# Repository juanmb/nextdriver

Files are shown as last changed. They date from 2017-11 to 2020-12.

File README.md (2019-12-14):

# NexStar Controller

A USB controller for [Celestron](https://www.celestron.com/collections/astronomy)
telescopes using the NexStar AUX protocol.

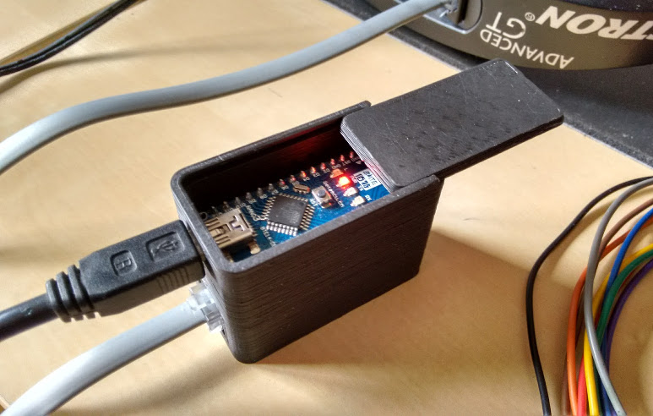
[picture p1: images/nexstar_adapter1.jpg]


## Description

This is a USB controller for Celestron NexStar AUX protocol implemented in Arduino.
It substitutes the hand controller, receiving the commands from the PC (HC procotol)
and communicating with the mount (AUX protocol).



Documentation on the NexStar HC and Aux protocols:

 * [NexStar HC Protocol](http://www.nexstarsite.com/download/manuals/NexStarCommunicationProtocolV1.2.zip)
 * [NexStar AUX Protocol](http://www.paquettefamily.ca/nexstar/NexStar_AUX_Commands_10.pdf)

## Features

 * Get/set location and time
 * Sync
 * Goto (equatorial and horizontal coordinates)
 * Tracking on/off
 * Meridian flip
 * Above-the-horizon limit

TODO:

 * RTC support
 * Homing switches
 * Hibernate/wakeup
 * Support for South hemisphere
 * Support for alt-az mounts

## Limitations

Currently, only equatorial mounts in the North hemisphere are supported.

## Required libraries

 * [Time](https://github.com/PaulStoffregen/Time)
 * [AccelStepper](https://github.com/waspinator/AccelStepper.git)

The library AstroLib, wich is part of this project, must be installed in the
Arduino libraries directory.

## Compiling

The provided Makefile requires [Arduino-Makefile](https://github.com/sudar/Arduino-Makefile)
to work. In Debian/Ubuntu/Mint, you can install it with

    sudo apt install arduino-mk

If you downloaded `Arduino-Makefile` to a custom location (other than
`/usr/share/arduino`), you must indicate the correct directory by modifying
the `ARDMK_DIR` variable in the `Makefile.avr` or `Makefile.sam`.

The code can be compiled and uploaded to the Arduino board using

    make
    make upload

Of course, you can also program the Arduino board using the Arduino IDE.

### Compiling for Arduino Due

Download the toolchain for SAM boards using the Boards Manager in the Arduino IDE.

Comment the line `include Makefile.avr` and discomment the line
`include Makefile.sam` in the `Makefile`.

## Schematics

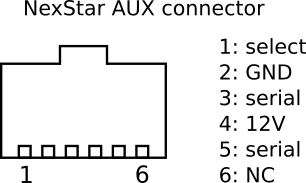
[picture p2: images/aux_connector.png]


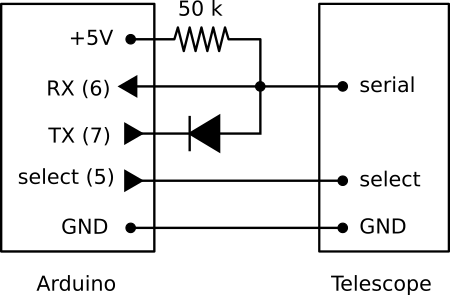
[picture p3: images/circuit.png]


## Enclosure

The CAD directory contains an STL model of the enclosure I use, which was
created with openSCAD. It requires an Arduino Nano and a small prototype
board. The resistor, the diode and the modular connector shown in the
schematics are mounted in the prototype board.

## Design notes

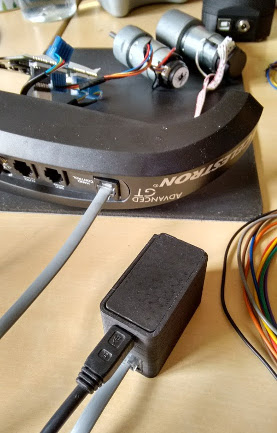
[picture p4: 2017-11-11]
images/nexstar_adapter2.jpg

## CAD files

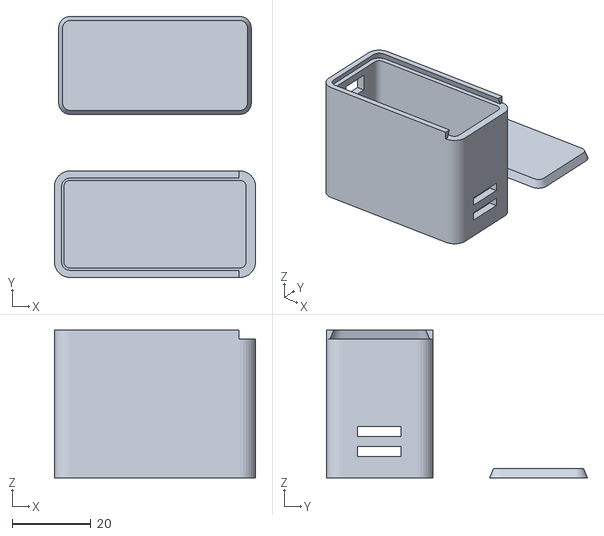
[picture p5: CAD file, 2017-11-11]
CAD/nexstar_adapter.stl
51.0 x 66.1 x 37.4

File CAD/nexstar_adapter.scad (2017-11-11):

thickness = 2.4;
size = [46+2*thickness, 22+2*thickness, 35];    // outer dimensions
connSize = [13, 13, 12.0];
usbSize = [8.5, 8.5, 5];
pcbThickness = 1.6;
connSize2 = [11, 11, 2.5];

$fn = 32;


module box(size, thickness, radius=4, tolerance=0.2, lid=false) {
    // some shorter aliases
    t = tolerance;
    th = thickness;
    r = radius;
    d = 2*r;

    // lid slope
    slope1 = 1.5;
    slope2 = 0.5;

    module outerCorner(x, y) {
        translate([(size[0] - d + t)*x, (size[1] - d + t)*y, 0])
            cylinder(size[2] + th, r=r);
    }

    module innerCorner(x, y) {
        translate([(size[0] - d + t)*x, (size[1] - d + t)*y, 0])
            cylinder(size[2], r=r-th);
    }

    module lidGrooveCorner(x, y) {
        translate([(size[0] - d + th - t)*x, (size[1] - d + t)*y, 0])
            cylinder(th, r - th + slope1, r - th + slope2);
    }

    module lidCorner(x, y) {
        translate([(size[0] - d + t)*x, (size[1] - d + t)*y, 0])
            cylinder(th, r - th + slope1 - t, r - th + slope2 - t);
    }

    translate([r, r, 0])
        if (lid) {
            // draw lid only
            hull() { for (i=[0, 1], j=[0, 1]) lidCorner(i, j); }
        } else {
            // draw box only
            difference () {
                hull() { for (i=[0, 1], j=[0, 1]) outerCorner(i, j); }

                translate([0, 0, th])
                    hull() { for (i=[0, 1], j=[0, 1]) innerCorner(i, j); }

                translate([0, 0, size[2] + t])
                    hull() { for (i=[0, 1], j=[0, 1]) lidGrooveCorner(i, j); }

                translate([size[0] - d, -r, size[2] + t])
                    cube([r, size[1] + t, th]);
            }
        }
}

module lid(size, thickness=2, radius=4, tolerance=0.2) {
    box(size, thickness, radius, tolerance, lid=true);
}

module pcbBox() {
    difference() {
        th = thickness;

        union() {
            translate([0, -size[1]/2, 0]) box(size, th);
        }
        // connectors
        usbPos = connSize[2] + pcbThickness + 4 + 8;
        translate([-.1, -usbSize[1]/2, th + usbPos]) cube(usbSize);
        translate([-.1, -connSize[1]/2, th]) cube(connSize);
        translate([size[0]-connSize2[0]/2, -connSize2[1]/2, th+3]) {
            cube(connSize2);
            translate([0, 0, 2.54*2]) cube(connSize2);
        }
    }
}

module wedge() {
    union() {
        cube([2.2, 12, 8]);
        cube([5.0, 12, 6]);
    }
}

pcbBox();
translate([0, size[1], 0]) lid(size, thickness);
//wedge();

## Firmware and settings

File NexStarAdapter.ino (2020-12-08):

/******************************************************************
    Author: Juan Menendez <juanmb@gmail.com>

    This code is part of the NexStarAdapter project:
        https://github.com/juanmb/NexStarAdapter

********************************************************************/

#ifdef __AVR__
#include <EEPROM.h>
#include <SoftwareSerial.h>
#else
#include <DueFlashStorage.h>
#endif
#include <TimeLib.h>
#include "serial_command.h"
#include "nexstar_aux.h"
#include "nexstar_stepper.h"
#include "AstroLib.h"

#define VERSION_MAJOR 4
#define VERSION_MINOR 21
#define MOUNT_MODEL 14  // CGEM DX
#define CONTROLLER_VARIANT 0x11  // NexStar
#define BAUDRATE 9600
#define GO_BELOW_HORIZON
#define ENABLE_HOMING
//#define DEBUG

// pin definitions
#define AUX_BUSY   2
#define AUX_SELECT 3
#define AUX_TX     4
#define AUX_RX     5
//#define DEBUG_TX 6

#define LED_STATUS_G 12 // synced/homed
#define LED_STATUS_R 13 // no time set
#define LED_RED      11 // error
#define LED_GREEN    10 // slewing
#define LED_YELLOW    9 // parked

#define HOME_BUTTON   7
#define ABORT_BUTTON   8
#define HOME_RA_PIN   A0
#define LIMIT_RA_PIN  A1
#define HOME_DEC_PIN  A2
#define LIMIT_ALT_PIN A3

//#define abs(x) (((x) > 0) ? (x) : -(x))
#define sign(x) (((x) > 0) ? 1 : -1)

#define decHomeSensor() (analogRead(HOME_DEC_PIN) > 512) // true if blocked
#define raHomeSensor() (analogRead(HOME_RA_PIN) > 512)   // true if blocked

#ifdef DEBUG
#define DEBUG_PRINT(x) debug.println(x)
#define DEBUG_FLOAT(x) debug.println(x, 6)
#else
#define DEBUG_PRINT(x) do {} while(0)
#define DEBUG_FLOAT(x) do {} while(0)
#endif

#ifdef __arm__
DueFlashStorage FS;
#endif

enum ScopeState {
    ST_IDLE,
    ST_MERIDIAN_FLIP,
    ST_SLEWING_FAST,
    ST_SLEWING_SLOW,
    ST_HOMING_DEC,
    ST_HOMING_FAST1,
    ST_HOMING_FAST2,
    ST_HOMING_SLOW1,
    ST_HOMING_SLOW2,
};

enum ScopeEvent {
    EV_NONE,
    EV_GOTO,
    EV_ABORT,
    EV_HOME,
};

enum PierSide {
    PIER_EAST,  // Mount on the east side of pier (looking west). Normal state
    PIER_WEST,  // Mount on the west side of pier (looking east)
};

struct AxisCoords {
    float ra;
    float dec;
};

ScopeState state = ST_IDLE;
ScopeEvent event = EV_NONE;

Location location = {0, 0};      // Default location
uint8_t tracking_mode = 0;
uint32_t ref_t = 0;    // millis() at last cmdSetTime call
double ref_lst = 0.0;  // Last synced LST
double ref_jd = 0.0;   // Last synced julian date refered to J2000
bool synced = false;
bool time_set = false;
bool aligned = false;
bool parked = false;
EqCoords target = {0};

// Addresses in EEPROM/Flash
#define ADDR_LOCATION 0
#define ADDR_HOME 2*4

SerialCommand sCmd;
NexStarAux nexstar(AUX_RX, AUX_TX, AUX_SELECT, AUX_BUSY);
//NexStarStepper nexstar;

#ifdef DEBUG
SoftwareSerial debug(DEBUG_TX);
#endif

// Get current Julian date
//static double getCurrentJD()
//{
    //return ref_jd + (double)(now() - ref_t)/(24.0*60*60);
//}

double normalizeAngle2pi(double h)
{
    int ih = (int)(h/2/M_PI);
    h = h - (double)ih*2*M_PI;
    return h < 0 ? h + 2*M_PI : h;
}

// Normalize an angle in radians between -pi and pi
double normalizeAngle(double h)
{
    h = normalizeAngle2pi(h);
    int ih = (int)(h/2/M_PI);
    h = h - (double)ih*2*M_PI;
    return h > M_PI ? h - 2*M_PI: h;
}

// Obtain current Local Sidereal Time from last synced time
// This is faster than performing the full calculation from JD & location
// by calling getLST()
double getCurrentLST() {
    return ref_lst + 2*M_PI*(double)(now() - ref_t)/(24.0*60*60);
}

// Convert nexstar angle format to radians
double nex2rad(uint16_t angle)
{
    return 2*M_PI*((double)angle / 0x10000);
}

// Convert nexstar precise angle format to radians
double pnex2rad(uint32_t angle)
{
    return 2*M_PI*((double)angle / 0x100000000);
}

// Convert radians to nexstar angle format
uint16_t rad2nex(double rad)
{
    return (uint16_t)(rad * 0x10000 / (2*M_PI));
}

// Convert radians to nexstar precise angle format
uint32_t rad2pnex(double rad)
{
    return (uint32_t)(rad * 0x100000000 / (2*M_PI));
}

/*****************************************************************************
  Coordinate conversions
******************************************************************************/

// Indicates the pointing state of the mount at a given position
// Reference: https://ascom-standards.org/Help/Platform/html/P_ASCOM_DeviceInterface_ITelescopeV3_SideOfPier.htm
PierSide getPierSide(AxisCoords ac)
{
    return normalizeAngle(ac.dec) < 0 ? PIER_WEST : PIER_EAST;
}

PierSide getPierSide()
{
    uint32_t int_dec;
    nexstar.getPosition(DEV_DEC, &int_dec);
    float dec = pnex2rad(int_dec);
    return normalizeAngle(dec) < 0 ? PIER_WEST : PIER_EAST;
}

// Convert mechanical coordinates to local coordinates (HA/dec)
void axisToLocalCoords(AxisCoords ac, LocalCoords *lc)
{
    //lc->ha = ac.ra + M_PI/2*(sign(ac.dec) - 1);
    //lc->dec = M_PI/2 - abs(ac.dec);
    lc->ha = ac.ra + M_PI/2*(sign(ac.dec) - 1);
    lc->dec = abs(ac.dec);
}

// Convert local coordinates (HA/dec) to mechanical coordinates
void localToAxisCoords(LocalCoords lc, AxisCoords *ac)
{
    ac->ra = lc.ha + M_PI/2*(1 - sign(lc.ha));
    ac->dec = (M_PI/2 - lc.dec)*sign(lc.ha);
}

// Convert local coordinates to equatorial coordinates
void localToEqCoords(LocalCoords lc, EqCoords *eq)
{
    eq->ra = normalizeAngle(getCurrentLST() - lc.ha);
    eq->dec = lc.dec;
}

// Convert equatorial coordinates to local coordinates
void eqToLocalCoords(EqCoords eq, LocalCoords *lc)
{
    lc->ha = normalizeAngle(getCurrentLST() - eq.ra);
    lc->dec = eq.dec;
}

// Convert equatorial coordinates to mechanical coordinates
void eqToAxisCoords(EqCoords eq, AxisCoords *ac)
{
    LocalCoords lc;
    eqToLocalCoords(eq, &lc);
    localToAxisCoords(lc, ac);
}

// Convert mechanical coordinates equatorial to coordinates
void axisToEqCoords(AxisCoords ac, EqCoords *eq)
{
    LocalCoords lc;
    axisToLocalCoords(ac, &lc);
    localToEqCoords(lc, eq);
}

/*****************************************************************************
  Get/set/goto position
******************************************************************************/

void getAxisCoords(AxisCoords *ac)
{
    uint32_t ra, dec;
    nexstar.getPosition(DEV_RA, &ra);
    nexstar.getPosition(DEV_DEC, &dec);

    ac->ra = normalizeAngle(pnex2rad(ra));
    ac->dec = normalizeAngle(pnex2rad(dec));
}

void getLocalCoords(LocalCoords *lc)
{
    AxisCoords ac;
    getAxisCoords(&ac);
    axisToLocalCoords(ac, lc);
}

void getEqCoords(EqCoords *eq)
{
    /*
    if (!synced) {
        *eq = {0, 0};
        return;
    }
    */
    LocalCoords lc;
    getLocalCoords(&lc);
    localToEqCoords(lc, eq);
}

void getHorizCoords(HorizCoords *hc)
{
    LocalCoords lc;
    getLocalCoords(&lc);
    localToHoriz(location, lc, hc);
}

void setAxisCoords(AxisCoords ac)
{
    nexstar.setPosition(DEV_RA, rad2pnex(ac.ra));
    nexstar.setPosition(DEV_DEC, rad2pnex(ac.dec));
    synced = true;
}

void setLocalCoords(LocalCoords lc)
{
    AxisCoords ac;
    localToAxisCoords(lc, &ac);
    setAxisCoords(ac);
}

void setEqCoords(EqCoords eq)
{
    AxisCoords ac;
    eqToAxisCoords(eq, &ac);
    setAxisCoords(ac);
}

void gotoAxisCoords(AxisCoords ac, bool slow)
{
    if (synced) {
        nexstar.gotoPosition(DEV_RA, slow, rad2pnex(ac.ra));
        nexstar.gotoPosition(DEV_DEC, slow, rad2pnex(ac.dec));
    }
}

void gotoEqCoords(EqCoords eq, bool slow)
{
    AxisCoords ac;
    eqToAxisCoords(eq, &ac);
    gotoAxisCoords(ac, slow);
}

void stopMotors()
{
    nexstar.move(DEV_RA, 0, 0);
    nexstar.move(DEV_DEC, 0, 0);
}

// Check if both axes have reached their target position
bool slewDone()
{
    bool ra_done, dec_done;

    nexstar.slewDone(DEV_RA, &ra_done);
    nexstar.slewDone(DEV_DEC, &dec_done);
    return ra_done && dec_done;
}

// Check if a meridian flip is required
bool checkMeridianFlip(EqCoords eq)
{
    AxisCoords ac;
    PierSide target_side, current_side;

    eqToAxisCoords(eq, &ac);
    target_side = getPierSide(ac);
    current_side = getPierSide();

    // A meridian flip is required if both angles have different sign
    return target_side != current_side;
}

void readLocation(Location *loc)
{
#ifdef __arm__
    byte *b1 = FS.readAddress(ADDR_LOCATION);
    memcpy(loc, b1, sizeof(Location));
#else
    EEPROM.get(ADDR_LOCATION, *loc);
#endif
}

// Store the location in EEPROM
void writeLocation(Location loc)
{
#ifdef __arm__
    byte b[sizeof(Location)];
    memcpy(b, &loc, sizeof(Location));
    FS.write(ADDR_LOCATION, b, sizeof(Location));
#else
    EEPROM.put(ADDR_LOCATION, loc);
#endif
}

// Read the home position from EEPROM
void readHomePosition(AxisCoords *ac)
{
#ifdef __arm__
    byte *b2 = FS.readAddress(ADDR_HOME);
    memcpy(ac, b2, sizeof(LocalCoords));
#else
    EEPROM.get(ADDR_HOME, *ac);
#endif
}

// Save current axis coordinates as the home position
void writeHomePosition()
{
    AxisCoords ac;
    getAxisCoords(&ac);

    // Store the home position in EEPROM
#ifdef __arm__
    byte b[sizeof(AxisCoords)];
    memcpy(b, &ac, sizeof(AxisCoords));
    FS.write(ADDR_HOME, b, sizeof(AxisCoords));
#else
    EEPROM.put(ADDR_HOME, ac);
#endif
}

/*****************************************************************************
  Serial commands
******************************************************************************/

void cmdGetEqCoords(char *cmd)
{
    EqCoords eq;
    getEqCoords(&eq);

    char tmp[19];

    if (cmd[0] == 'E')
        sprintf(tmp, "%04X,%04X#", rad2nex(eq.ra), rad2nex(eq.dec));
    else
        sprintf(tmp, "%08lX,%08lX#", rad2pnex(eq.ra), rad2pnex(eq.dec));

    Serial.write(tmp);
}

void cmdGetAzCoords(char *cmd)
{
    HorizCoords hc;
    getHorizCoords(&hc);

    char tmp[19];

    if (cmd[0] == 'Z')
        sprintf(tmp, "%04X,%04X#", rad2nex(hc.az), rad2nex(hc.alt));
    else
        sprintf(tmp, "%08lX,%08lX#", rad2pnex(hc.az), rad2pnex(hc.alt));

    Serial.write(tmp);
}

void cmdGetPierSide(char *cmd)
{
    // Celestron protocol use the opposite definition of pier side
    Serial.write(getPierSide() == PIER_EAST ? 'W' : 'E');
    Serial.write('#');
}

void cmdSyncEqCoords(char *cmd)
{
    EqCoords eq;

    if (cmd[0] == 'S') {
        uint16_t ra, dec;
        sscanf(cmd + 1, "%4hx,%4hx", &ra, &dec);
        eq.ra = nex2rad(ra);
        eq.dec = nex2rad(dec);
    } else {
        uint32_t ra, dec;
        sscanf(cmd + 1, "%8lx,%8lx", &ra, &dec);
        eq.ra = pnex2rad(ra);
        eq.dec = pnex2rad(dec);
    }

    setEqCoords(eq);
    Serial.write('#');
}

void cmdGotoEqCoords(char *cmd)
{
    EqCoords eq;

    if (cmd[0] == 'R') {
        uint16_t ra, dec;
        sscanf(cmd + 1, "%4hx,%4hx", &ra, &dec);
        eq.ra = nex2rad(ra);
        eq.dec = nex2rad(dec);
    } else {
        uint32_t ra, dec;
        sscanf(cmd + 1, "%8lx,%8lx", &ra, &dec);
        eq.ra = pnex2rad(ra);
        eq.dec = pnex2rad(dec);
    }

#ifdef GO_BELOW_HORIZON
    target.ra = eq.ra;
    target.dec = eq.dec;
    event = EV_GOTO;
#else
    // Obtain the horizontal coordinates of the target
    LocalCoords lc;
    HorizCoords hc;
    eqToLocalCoords(eq, &lc);
    localToHoriz(location, lc, &hc);

    // If target is above the horizon, go
    if (hc.alt >= 0) {
        target.ra = eq.ra;
        target.dec = eq.dec;
        event = EV_GOTO;
    }
#endif
    Serial.write('#');
}

void cmdGotoAzCoords(char *cmd)
{
    HorizCoords hc;

    if (cmd[0] == 'B') {
        uint16_t az, alt;
        sscanf(cmd + 1, "%4hx,%4hx", &az, &alt);
        hc.az = nex2rad(az);
        hc.alt = nex2rad(alt);
    } else {
        uint32_t az, alt;
        sscanf(cmd + 1, "%8lx,%8lx", &az, &alt);
        hc.az = pnex2rad(az);
        hc.alt = pnex2rad(alt);
    }

    if (hc.alt >= 0) {
        // If target is above the horizon, go
        LocalCoords lc;
        horizToLocal(location, hc, &lc);
        localToEqCoords(lc, &target);
        event = EV_GOTO;

#ifdef ENABLE_HOMING
        // Home the mount if az=0, alt=0
        if (hc.az == 0 && hc.alt == 0) {
            event = EV_HOME;
        }
#endif
    }
    Serial.write('#');
}

void cmdIsAligned(char *cmd)
{
    Serial.write(aligned ? '1' : '0');
    Serial.write('#');
}

void cmdGotoInProgress(char *cmd)
{
    Serial.write(state == ST_IDLE ? '0' : '1');
    Serial.write('#');
}

void cmdCancelGoto(char *cmd)
{
    event = EV_ABORT;
    Serial.write('#');
}

void cmdGetTrackingMode(char *cmd)
{
    Serial.write(tracking_mode);
    Serial.write('#');
}

void cmdSetTrackingMode(char *cmd)
{
    //TODO: store tracking mode in EEPROM and engage tracking at start
    tracking_mode = cmd[1];
    nexstar.setGuiderate(DEV_RA, GUIDERATE_POS, true, 0);    // stop RA motor
    nexstar.setGuiderate(DEV_DEC, GUIDERATE_POS, true, 0);   // stop DEC motor

    switch(tracking_mode) {
        case TRACKING_EQ_NORTH:
            nexstar.setGuiderate(DEV_RA, GUIDERATE_POS, 0, GUIDERATE_SIDEREAL);
            break;
        case TRACKING_EQ_SOUTH:
            nexstar.setGuiderate(DEV_RA, GUIDERATE_NEG, 0, GUIDERATE_SIDEREAL);
            break;
    }

    Serial.write('#');
}

void cmdGetLocation(char *cmd)
{
    SxAngle sxLat, sxLong;

    rad2sx(location.latitude, &sxLat);
    Serial.write(sxLat.deg);
    Serial.write(sxLat.min);
    Serial.write(sxLat.sec);
    Serial.write(sxLat.sign);

    rad2sx(location.longitude, &sxLong);
    Serial.write(sxLong.deg);
    Serial.write(sxLong.min);
    Serial.write(sxLong.sec);
    Serial.write(sxLong.sign);
    Serial.write('#');
}

void cmdSetLocation(char *cmd)
{
    SxAngle latitude = {
        (uint8_t)cmd[1], (uint8_t)cmd[2],
        (uint8_t)cmd[3], (uint8_t)cmd[4]
    };

    SxAngle longitude = {
        (uint8_t)cmd[5], (uint8_t)cmd[6],
        (uint8_t)cmd[7], (uint8_t)cmd[8]
    };

    float lat = sx2rad(latitude);
    float lon = sx2rad(longitude);

    if ((lat != location.latitude) || (lon != location.longitude)) {
        location.latitude = sx2rad(latitude);
        location.longitude = sx2rad(longitude);

        ref_lst = getLST(now(), location);
        synced = false;

	writeLocation(location);
    }

    Serial.write('#');
}

void cmdSetTime(char *cmd)
{
    int hour = (int)cmd[1];
    int min = (int)cmd[2];
    int sec = (int)cmd[3];
    int month = (int)cmd[4];
    int day = (int)cmd[5];
    int year = (int)cmd[6] + 2000;
    int offset = (int)cmd[7];
    //int dst = (int)cmd[8];

    setTime(hour, min, sec, day, month, year);
    adjustTime(-offset*3600);

    ref_t = now();
    ref_lst = getLST(ref_t, location);
    time_set = true;
    synced = false;

    Serial.write('#');
}

void cmdGetTime(char *cmd)
{
    time_t t = now();
    Serial.write(hour(t));
    Serial.write(minute(t));
    Serial.write(second(t));
    Serial.write(month(t));
    Serial.write(day(t));
    Serial.write(year(t) % 2000);
    Serial.write((uint8_t)0);
    Serial.write((uint8_t)0);
    Serial.write("#");
}

void cmdPassThrough(char *cmd)
{
    char resp[8];
    uint8_t size;

    if (nexstar.sendRawCommand(cmd, resp, &size) == 0) {
        for (int i=0; i < size; i++) {
            Serial.write(resp[i]);
        }
    } else {
        // indicate an error by returning a response of size = resp_size + 1
        for (int i=0; i <= size; i++) {
            Serial.write('0');
        }
    }

    Serial.write('#');
}

void cmdGetVersion(char *cmd)
{
    Serial.write(VERSION_MAJOR);
    Serial.write(VERSION_MINOR);
    Serial.write('#');
}

void cmdGetVariant(char *cmd)
{
    Serial.write(CONTROLLER_VARIANT);
    Serial.write('#');
}

void cmdGetModel(char *cmd)
{
    Serial.write(MOUNT_MODEL);
    Serial.write('#');
}

void cmdEcho(char *cmd)
{
    Serial.write(cmd[1]);
    Serial.write('#');
}

void cmdHibernate(char *cmd)
{
    //TODO
}

void cmdWakeup(char *cmd)
{
    //TODO
    Serial.write('#');
}

void setup()
{
    // Map serial commands to functions
    sCmd.addCommand('E', 1, cmdGetEqCoords);
    sCmd.addCommand('e', 1, cmdGetEqCoords);
    sCmd.addCommand('Z', 1, cmdGetAzCoords);
    sCmd.addCommand('z', 1, cmdGetAzCoords);
    sCmd.addCommand('p', 1, cmdGetPierSide);

    sCmd.addCommand('S', 10, cmdSyncEqCoords);
    sCmd.addCommand('s', 18, cmdSyncEqCoords);

    sCmd.addCommand('R', 10, cmdGotoEqCoords);
    sCmd.addCommand('r', 18, cmdGotoEqCoords);

    sCmd.addCommand('B', 10, cmdGotoAzCoords);
    sCmd.addCommand('b', 18, cmdGotoAzCoords);

    sCmd.addCommand('L', 1, cmdGotoInProgress);
    sCmd.addCommand('M', 1, cmdCancelGoto);
    sCmd.addCommand('J', 1, cmdIsAligned);

    sCmd.addCommand('T', 2, cmdSetTrackingMode);
    sCmd.addCommand('t', 1, cmdGetTrackingMode);

    sCmd.addCommand('W', 9, cmdSetLocation);
    sCmd.addCommand('w', 1, cmdGetLocation);
    sCmd.addCommand('H', 9, cmdSetTime);
    sCmd.addCommand('h', 1, cmdGetTime);

    sCmd.addCommand('P', 8, cmdPassThrough);
    sCmd.addCommand('V', 1, cmdGetVersion);
    sCmd.addCommand('v', 1, cmdGetVariant);
    sCmd.addCommand('m', 1, cmdGetModel);
    sCmd.addCommand('K', 2, cmdEcho);

    //sCmd.addCommand('J', 1, cmdAlignmentComplete);
    sCmd.addCommand('x', 1, cmdHibernate);
    sCmd.addCommand('y', 1, cmdWakeup);

    pinMode(AUX_SELECT, OUTPUT);
    //pinMode(LED_BUILTIN, OUTPUT);
    pinMode(LED_STATUS_R, OUTPUT);
    pinMode(LED_STATUS_G, OUTPUT);
    pinMode(LED_RED, OUTPUT);
    pinMode(LED_GREEN, OUTPUT);
    pinMode(LED_YELLOW, OUTPUT);

    pinMode(HOME_BUTTON, INPUT_PULLUP);
    pinMode(ABORT_BUTTON, INPUT_PULLUP);
    pinMode(LIMIT_RA_PIN, INPUT_PULLUP);
    pinMode(LIMIT_ALT_PIN, INPUT_PULLUP);

#ifdef DEBUG
    debug.begin(9600);
#endif
    Serial.begin(BAUDRATE);
    nexstar.init();

    // read location and home position from EEPROM
    readLocation(&location);

    //AxisCoords home_pos;
    //readHomePosition(&home_pos);
    AxisCoords home_pos={M_PI/2, M_PI/2};
    setAxisCoords(home_pos);

    nexstar.setGuiderate(DEV_RA, GUIDERATE_POS, true, 0);    // stop RA motor
    nexstar.setGuiderate(DEV_DEC, GUIDERATE_POS, true, 0);   // stop DEC motor
}
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
void loop()
{
    if (!digitalRead(ABORT_BUTTON) && state != ST_IDLE)
        event = EV_ABORT;
    else if (!digitalRead(HOME_BUTTON) && state != ST_HOMING_DEC)
        event = EV_HOME;

    sCmd.readSerial();
    updateFSM();
    updateLEDs();
    nexstar.run();
}

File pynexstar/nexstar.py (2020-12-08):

from math import pi
import struct
import serial
import time
import ephem

# device IDs:
MAIN_DEV = 0x01
HC_DEV = 0x04
RA_DEV = 0x10
DEC_DEV = 0x11
GPS_DEV = 0xb0
RTC_DEV = 0xb2


def to_hex(data):
    return ' '.join(['%02X' % ord(c) for c in data])


def nex2rad(angle, precise=False):
    max_value = 0x100000000 if precise else 0x10000
    return angle*2*pi/max_value


def normalize_angle(h):
    ih = int(h/2/pi)
    h = h - ih*2*pi
    return h + 2*pi if h < 0 else h


def rad2nex(angle, precise=False):
    angle = normalize_angle(angle)
    max_value = 0x100000000 if precise else 0x10000
    if angle < 0:
        angle += 2*pi
    return int(angle*max_value/(2*pi))


def normalize_dec(angle):
    if angle > pi:
        return angle - 2*pi
    return angle


class NexStar(object):
    def __init__(self, port, debug=False):
        self.debug = debug
        self.serial = serial.Serial(port, 9600, timeout=1.0)
        self.serial.flushInput()
        #print "Wait until Arduino is ready..."
        time.sleep(2)

    def close(self):
        self.serial.close()

    def send_packet(self, data, resp_len):
        if self.debug:
            print("Sent:", to_hex(data) if data[0] in 'PWH' else data)
        self.serial.write(data)
        self.serial.flushInput()
        resp = self.serial.read(resp_len)
        if self.debug:
            print("Recv:", resp if data[0] in 'eEzZ' else to_hex(resp))
        return resp

    def send_passthrough(self, dest, Id, payload='', resp_len=0):
        if len(payload) > 4:
            raise ValueError("Invalid payload size")

        length = len(payload) + 1
        fill = '\0'*(3 - len(payload))
        fmt = 'cBBB%ds%dsB' % (len(payload), len(fill))
        data = struct.pack(fmt, 'P', length, dest, Id, payload, fill, resp_len-1)
        return  self.send_packet(data, resp_len)

    def get_version(self):
        ret = self.send_packet('V', 3)
        return '%d.%02d' % (ord(ret[0]), ord(ret[1]))

    def get_variant(self):
        ret = self.send_packet('v', 3)
        return ret[0]

    def get_model(self):
        ret = self.send_packet('m', 2)
        return ord(ret[0])

    def echo(self, char):
        ret = self.send_packet('K%c' % char, 2)
        return ret[0]

    def get_device_version(self, dest):
        ret = self.send_passthrough(dest, 0xfe, resp_len=3)
        return '%d.%02d' % (ord(ret[0]), ord(ret[1]))

    def slew_ra(self, rate, direction):
        _id = 0x24 if direction else 0x25
        payload = struct.pack('B', rate)
        self.send_passthrough(RA_DEV, _id, payload)

    def get_eq_coords(self, precise=False):
        '''Get equatorial coords in radians'''
        if precise:
            ret = self.send_packet('e', 18)
        else:
            ret = self.send_packet('E', 10)

        ra, dec = [int(a, 16) for a in ret.strip('#').split(',')]
        return nex2rad(ra, precise), normalize_dec(nex2rad(dec, precise))

    def get_az_coords(self, precise=False):
        if precise:
            ret = self.send_packet('z', 18)
        else:
            ret = self.send_packet('Z', 10)

        az, alt = [int(a, 16) for a in ret.strip('#').split(',')]
        return nex2rad(az, precise), normalize_dec(nex2rad(alt, precise))

    def sync_eq_coords(self, ra, dec, precise=False):
        coords = rad2nex(ra, precise), rad2nex(dec, precise)
        if precise:
            self.send_packet('s%08X,%08X' % coords, 1)
        else:
            self.send_packet('S%04X,%04X' % coords, 1)

    def goto_eq_coords(self, ra, dec, precise=False):
        coords = rad2nex(ra, precise), rad2nex(dec, precise)
        if precise:
            self.send_packet('r%08X,%08X' % coords, 1)
        else:
            self.send_packet('R%04X,%04X' % coords, 1)

    def sync_home_position(self):
        self.send_packet('i', 1)

    def set_location(self, lat, lon):
        ''' Set location in radians '''
        lat = ephem.degrees(lat)
        lon = ephem.degrees(lon)

        lat_split = [int(float(s)) for s in str(lat).split(':')]
        lon_split = [int(float(s)) for s in str(lon).split(':')]
        lat_sign = int(lat_split[0] < 0)
        lon_sign = int(lon_split[0] < 0)
        lat_split[0] = abs(lat_split[0])
        lon_split[0] = abs(lon_split[0])

        args = lat_split + [lat_sign] + lon_split + [lon_sign]
        payload = struct.pack('8B', *args)
        self.send_packet('W%s' % payload, 1);

    def get_location(self):
        ret = self.send_packet('w', 9)
        lat_deg, lat_min, lat_sec, lat_sign, lon_deg, lon_min, lon_sec, lon_sign, _ = \
            struct.unpack('BBBBBBBBB', ret)

        if lat_sign:
            lat_deg *= -1

        if lon_sign:
            lon_deg *= -1

        lat = '%d:%d:%d' % (lat_deg, lat_min, lat_sec)
        lon = '%d:%d:%d' % (lon_deg, lon_min, lon_sec)
        return ephem.degrees(lat).real, ephem.degrees(lon).real

    def set_time(self, date_str):
        t = time.strptime(date_str, '%Y/%m/%d %H:%M:%S')
        payload = struct.pack('BBBBBBBB', t.tm_hour, t.tm_min, t.tm_sec,
                              t.tm_mon, t.tm_mday, t.tm_year % 2000, 0, 0)
        self.send_packet('H%s' % payload, 1);

    def get_time(self):
        ret = self.send_packet('h', 9)
        h, m, s, M, D, Y, offset, dst, _ = struct.unpack('BBBBBBBBB', ret)
        return '%d/%d/%d %d:%d:%d +%03d' % (2000+Y, M, D, h, m, s, offset)

    def cancel_goto(self):
        self.send_packet('M', 1)

    def hibernate(self):
        self.send_packet('x', 1)

    def is_slewing(self):
        ret = self.send_packet('L', 2)
        return ret[0] != '0'

    def is_aligned(self):
        ret = self.send_packet('J', 2)
        return ret[0] != '0'

    def get_tracking_mode(self):
        ret = self.send_packet('t', 2)
        return ord(ret[0])

    def set_tracking_mode(self, mode=0):
        self.send_packet('T%c' % mode, 1)
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

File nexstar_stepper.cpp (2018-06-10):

/******************************************************************
    Author:     Juan Menendez Blanco    <juanmb@gmail.com>

    This code is part of the NexStarAdapter project:
        https://github.com/juanmb/NexStarAdapter

*******************************************************************/

#include <Arduino.h>
#include "nexstar_stepper.h"

#define VERSION_MAJOR 3
#define VERSION_MINOR 4

// Motor parameters
#define GEAR_RATIO 1
#define STEPS 200
#define MICROSTEPS 16
#define USTEPS_REV (GEAR_RATIO*STEPS*MICROSTEPS) // microsteps per revolution
#define POS_FACTOR (0x100000000L/USTEPS_REV)

#define GOTO_SPEED 800
#define ACCEL 800

// CNC Shield pins
#define XSTEP 2
#define YSTEP 3
#define ZSTEP 4
#define XDIR 5
#define YDIR 6
#define ZDIR 7
#define ENABLE 8
#define XSTOP 9
#define YSTOP 10
#define ZSTOP 11
#define SPINDLE_ENABLE 12
#define SPINDLE_DIR 13

// Photodiode pin
#define PHOTO_PIN ZSTEP


NexStarStepper::NexStarStepper(void) :
    azMotor(AccelStepper::DRIVER, XSTEP, XDIR),
    altMotor(AccelStepper::DRIVER, YSTEP, YDIR)
{
}

// Initialize pins and setup serial port
void NexStarStepper::init()
{
    // Enable pin
    pinMode(ENABLE, OUTPUT);
    // Configure outputs
    pinMode(XSTEP, OUTPUT);
    pinMode(XDIR, OUTPUT);
    pinMode(YSTEP, OUTPUT);
    pinMode(YDIR, OUTPUT);
    // Photo diode pin
    pinMode(PHOTO_PIN, INPUT);

    // Configure axes logic and dynamics
    azMotor.setPinsInverted(true, false, true);
    azMotor.setAcceleration(ACCEL);
    azMotor.setEnablePin(ENABLE);

    altMotor.setPinsInverted(false, false, true);
    altMotor.setAcceleration(ACCEL);
    altMotor.setEnablePin(ENABLE);

    digitalWrite(ENABLE, HIGH);
}

int NexStarStepper::setPosition(uint8_t dest, uint32_t pos)
{
    AccelStepper *motor = (dest == DEV_AZ) ? &azMotor : &altMotor;

    motor->setCurrentPosition(pos/POS_FACTOR);
    return 0;
}

int NexStarStepper::getPosition(uint8_t dest, uint32_t *pos)
{
    AccelStepper *motor = (dest == DEV_AZ) ? &azMotor : &altMotor;

    long motorPos = motor->currentPosition();
    *pos = motorPos*POS_FACTOR;
    return 0;
}

// Obtain the relative distance for travelling to the target position
long getDiff(long cur, long tgt)
{
    cur = (cur < USTEPS_REV/2) ? cur : cur - USTEPS_REV;
    tgt = (tgt < USTEPS_REV/2) ? tgt : tgt - USTEPS_REV;
    return tgt - cur;
}

int NexStarStepper::gotoPosition(uint8_t dest, bool slow, uint32_t pos)
{
    AccelStepper *motor = (dest == DEV_AZ) ? &azMotor : &altMotor;

    digitalWrite(ENABLE, LOW);
    motor->setMaxSpeed(GOTO_SPEED);

    long current = motor->currentPosition();
    long target = pos/POS_FACTOR;

    motor->move(getDiff(current, target));
    return 0;
}

int NexStarStepper::move(uint8_t dest, bool dir, uint8_t rate)
{
    AccelStepper *motor = (dest == DEV_AZ) ? &azMotor : &altMotor;
    long pos = dir ? USTEPS_REV/2 : -USTEPS_REV/2;

    if (rate == 0) {
        motor->stop();
    } else {
        digitalWrite(ENABLE, LOW);
        motor->setMaxSpeed(10*rate);
        motor->move(pos);
    }
    return 0;
}

int NexStarStepper::slewDone(uint8_t dest, bool *done)
{
    AccelStepper *motor = (dest == DEV_AZ) ? &azMotor : &altMotor;

    *done = !motor->isRunning();
    return 0;
}

int NexStarStepper::setGuiderate(uint8_t dest, bool dir, bool custom_rate, uint32_t rate)
{
    return 0;
}

int NexStarStepper::getVersion(uint8_t dest, char *major, char *minor)
{
    *major = VERSION_MAJOR;
    *minor = VERSION_MINOR;
    return 0;
}

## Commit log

2017-11-01 Fix Goto and getTime commands
    [NexStarAdapter.ino]
2017-11-06 Apply tracking corrections to RA position
    [NexStarAdapter.ino, nexstar_aux.cpp]
2017-11-11 Add some images and CAD files
    [nexstar_adapter.scad, nexstar_adapter.stl]
2018-05-22 Precise LST calculation. Implement meridian flip
    [NexStarAdapter.ino, nexstar.py]
2018-05-23 Correct motor direction on 'goto' in nexstar_stepper
    [nexstar_stepper.cpp]
2018-05-23 Fix getEqCoords. Ignore goto below the horizon
    [NexStarAdapter.ino]
2018-06-10 Fix normalization of negative angles
    [NexStarAdapter.ino, nexstar.py, nexstar_stepper.cpp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]
2018-06-17 Go to the pole when performing a meridian flip
    [NexStarAdapter.ino]
2018-08-15 Home the mount when target is az=0 alt=0
2018-08-18 Fix homing procedure
2018-08-20 Fix homing. Serial debugging
    [NexStarAdapter.ino]
2018-08-25 Fix bug in getPierSide
    [NexStarAdapter.ino, nexstar.py]
2018-08-28 Change the polarity of the RA home sensor
2019-06-09 Return RA,dec=0,0 when not synced. Set synced=false after homing
2019-06-09 Change home sensor polarity
2019-12-14 Add support for Arduino Due
2020-07-03 Arduino UNO pin definitions
2020-07-04 Control LEDs and buttons
